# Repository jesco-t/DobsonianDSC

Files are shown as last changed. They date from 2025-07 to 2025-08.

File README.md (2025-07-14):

# Digital Setting Circles for a Manual Telescope Mount.

Design and code based on this GitHub project https://github.com/vlaate/DobsonianDSC. Code is converted to PlatformIO and a few bugs fixed (mostly due to newer dependencies having deprecated some usage patterns). A discussion thread on CloudyNights can be found here https://www.cloudynights.com/topic/589521-37-dobsonian-dsc-for-diy-makers/.

The PCB is designed for the NodeMCU DevKit C module. It is my own design.

The CAD files for the 10" Meade Lightbride are my own original design.
## PCB

The PCB is designed for the NodeMCU DevKit C. It uses 12V DC as power supply which should be readily available. It uses a 100uF input capacitor and 5V DC/DC converter to supply a stable voltage to the encoders. The ESP32 is not 5V tolerant on its GPIO pins which requires the 4-channel level shifter between NodeMCU and the encoders. 

The connectors to the encoders are JST-XH, which require a special crimp tool and some practice. The tool is extra 30€ or so but it’s well worth it in my opinion. The pinning is `+5V, GND, A, B, Shield/GND`.

The case for the board is a marginal fit because the screw holes are off by a few hundred micron. Apologies. If you want to fix it, I recommend updating the board layout in KiCAD and not the case in FreeCAD. It’s the board that has the odd measurements.

The Gerber files in the repository are suitable for JLPCB which I can highl recommend. A set of 5 boards cost me <10€.

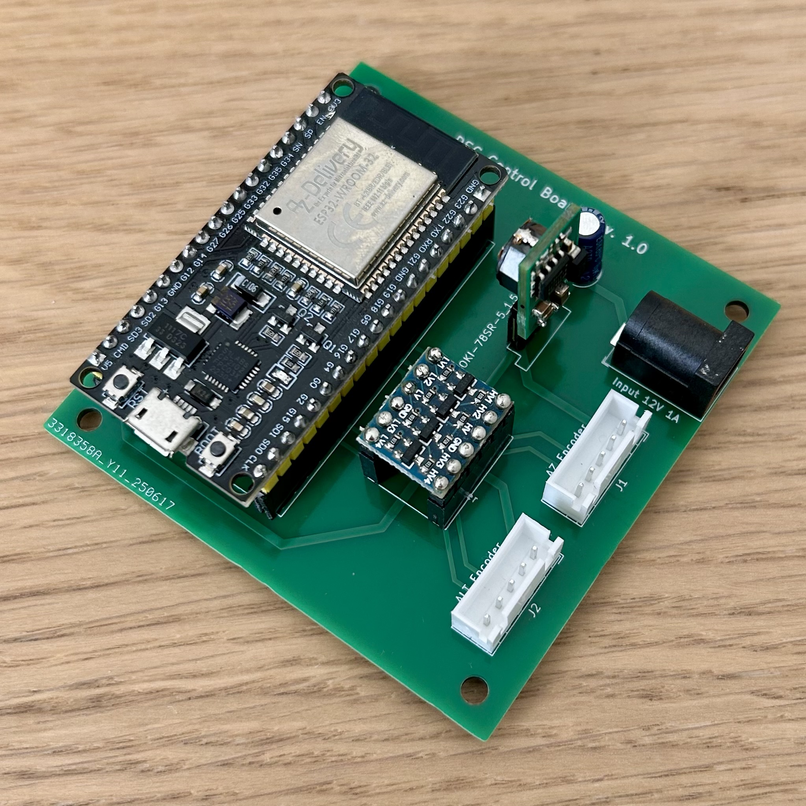
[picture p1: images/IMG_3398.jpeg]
PCB


## Software

The software needs to be compiled and uploaded with PlatformIO. Like the ArduinoIDE it's free. You need to install VSCode and the the PlatformIO extension. There are no changes needed to upload.
## Modifications on the 10" Meade Lightbridge

I use a gear driven mechanism for the encoder train. I decided against belts because the altitude axis needs to be easily to dismantle. The azimuth axis uses the same gear ratio. 

## Altitude Axis

The altitude gear is attached in three pieces: a mounting ring is glued onto the metal trunnion. The mounting ring has 4x M3 heat inserts. Then a spacer ring and the gear ring is threaded on with M3 screws.

The encoder is screwed into its mount. The encoder gear is loosely slid over the encoder and the proper spacing to the axis gear is determined. The gears should mesh well with a bit but not too much play. Mark the position and screw the encoder mount onto the base.

The axis gear has 155 teeth and the Encoder gear has 62. With 2400 pulses on the quadrature encoder this makes for 6000 steps across a 360° totation of the axis.

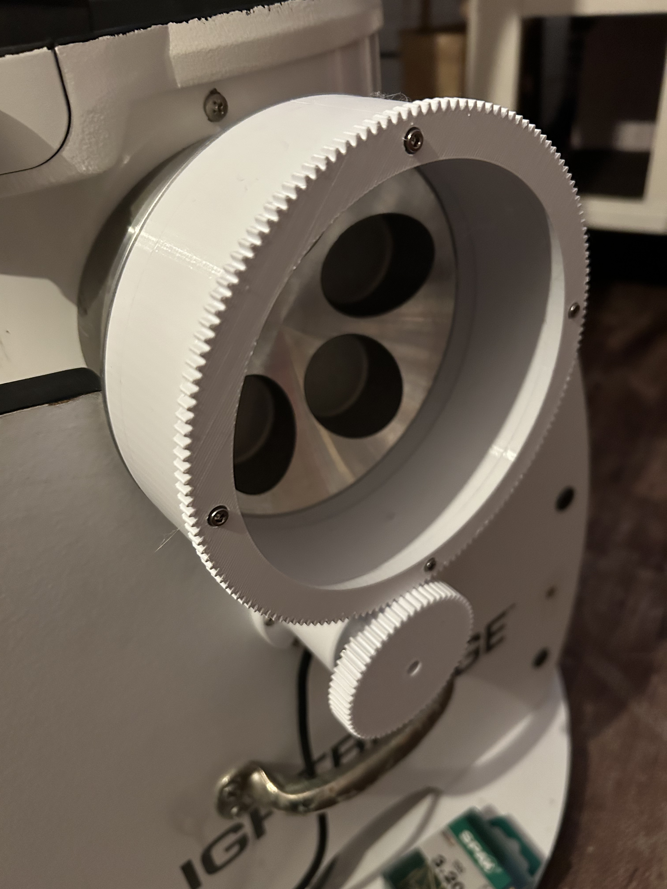
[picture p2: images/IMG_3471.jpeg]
altitude axis


## Azimuth Axis

The azimuth gear is mounted in the azimuth tension knob. It's held onto the knob with four M3 screws. The setup is the same as the altitude gear: mounting ring, spacer and then the actual gear. Here, the spacer and gear are attached with individual screws.

The encoder is attached in a similar fashion than the altitude encoder. The gear itself is mounted reverse compared to the altitude axis. For the AZ gear, use the same STL file as-is for ALT gear on the encoder. Use your slicer to remove the upper 5mm of the gear so that the height of the gear mesh is correct.

The axis gear has 155 teeth and the Encoder gear has 62. With 2400 pulses on the quadrature encoder this makes for 6000 steps across a 360° totation of the axis.

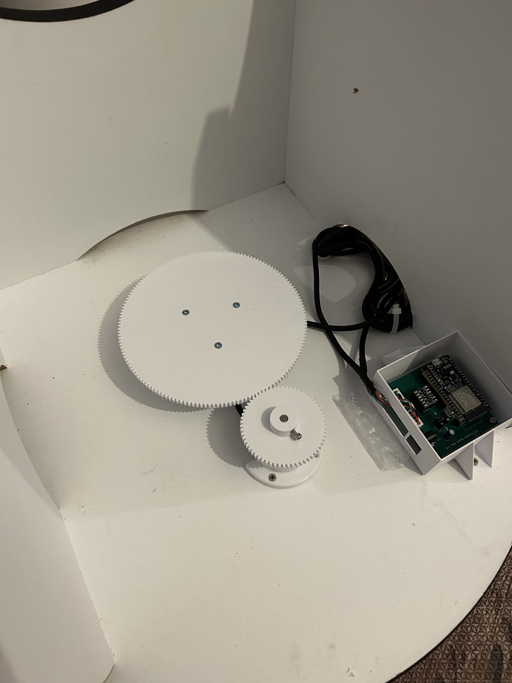
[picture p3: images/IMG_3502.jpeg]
azimuth axis


## Bill-of-Materials

| Module  | Item | Pieces | Description |
| --- | --- | --- | --- |
| PCB | NodeMCU DevKit C | 1 | |
| PCB | OKI-SR78-5/1.5-W36-C | 1 | 5V DC/DC converter |
| PCB | Capacitor (100uF/>25V) | 1 | 47uF is also ok |
| PCB | 4-Channel Level Shifter 5V~3.3V | 1 | needs VC/GND in the middle |
| PCB | JST-XH 2.54 Plug & Socket | 2 | need crimp tool also |
| PCB | 5.5x2.1 DC Socket | 1 | |
| Encoder | 600 steps A/B Encoder | 2 | |
| Misc | M3 Screw Set | 1 | |
| Misc | M3 Heat Insets | 20 | |
| Misc | 3x20 Wood Screws | 8 | |

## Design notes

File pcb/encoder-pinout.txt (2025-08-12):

Red - VCC
Black 0V
Green - A
White - B
(Yellow - Z)
(Brown - -A)
(Gray - -B)
(Orange - -Z)
Shield

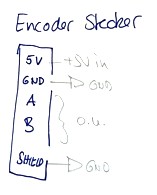
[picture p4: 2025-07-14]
pcb/encoder-pinout.jpg

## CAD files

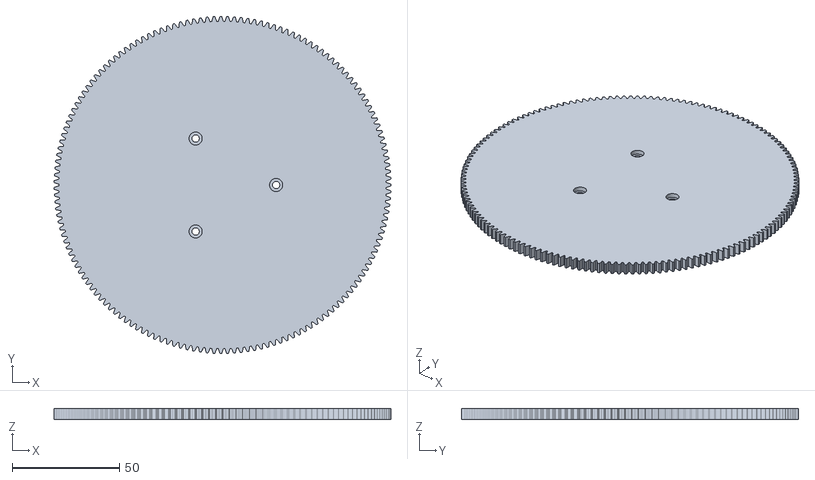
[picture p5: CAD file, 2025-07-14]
encoder_mounts/meade_lightbridge_10/AZ_Gear.stl
157.0 x 157.0 x 5.00

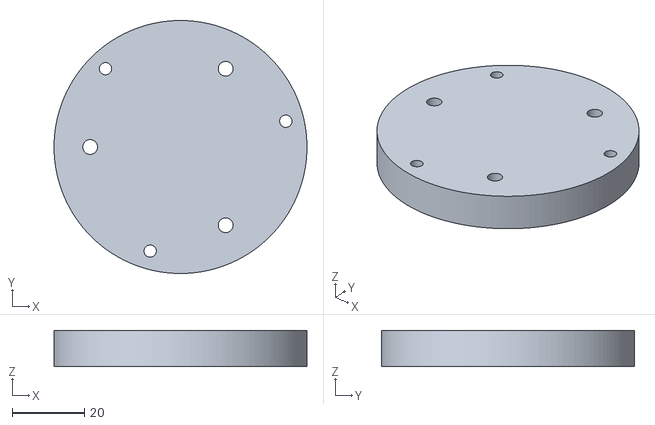
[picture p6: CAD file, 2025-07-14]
encoder_mounts/meade_lightbridge_10/STL/AZ_Spacer.stl
70.0 x 70.0 x 10.0

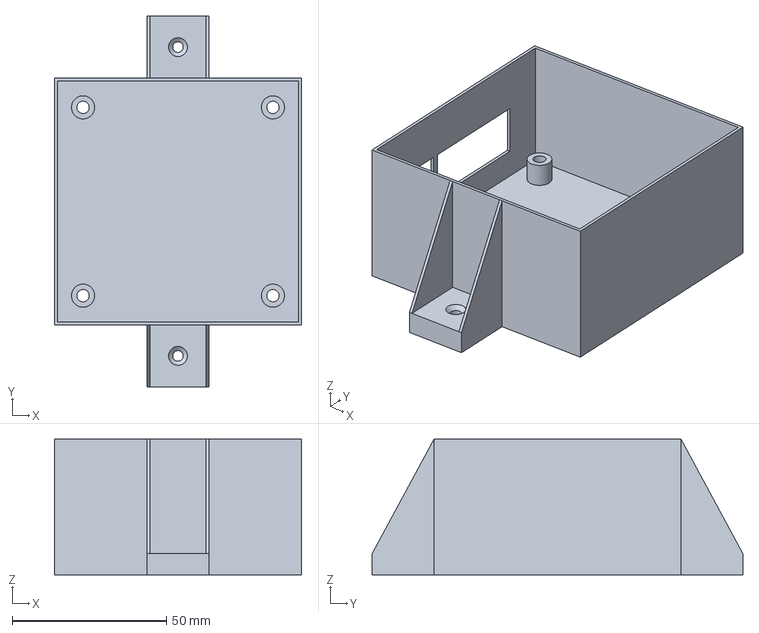
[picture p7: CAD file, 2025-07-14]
pcb/CAD/DSC-Board-Case.FCStd
80.0 x 120.0 x 44.0 mm

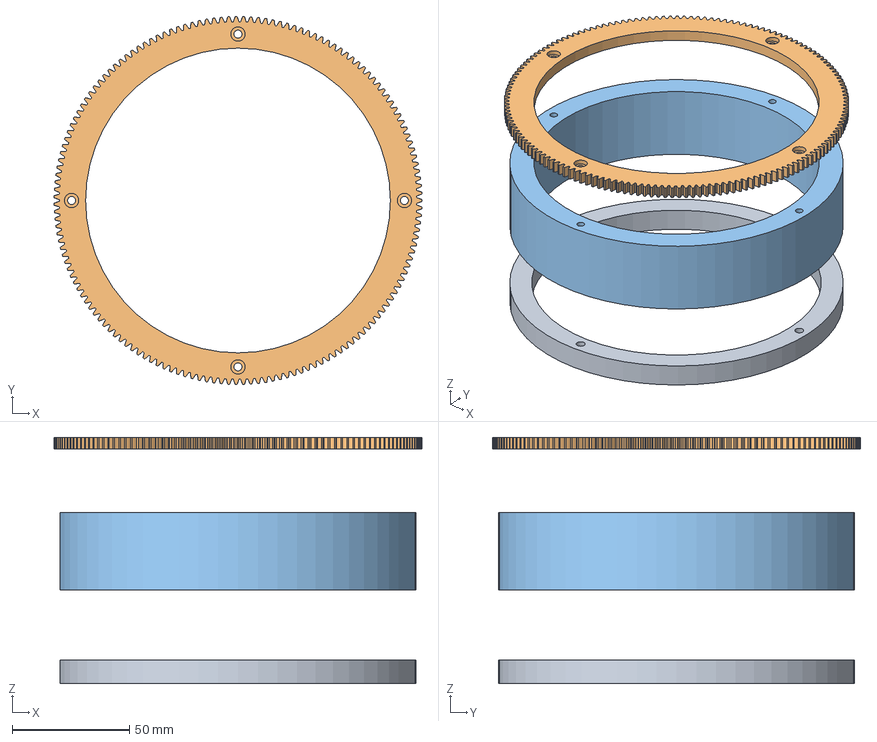
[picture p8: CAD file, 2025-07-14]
encoder_mounts/meade_lightbridge_10/ALT.FCStd
157.0 x 157.0 x 105.0 mm
Mounting
Gear
Spacer

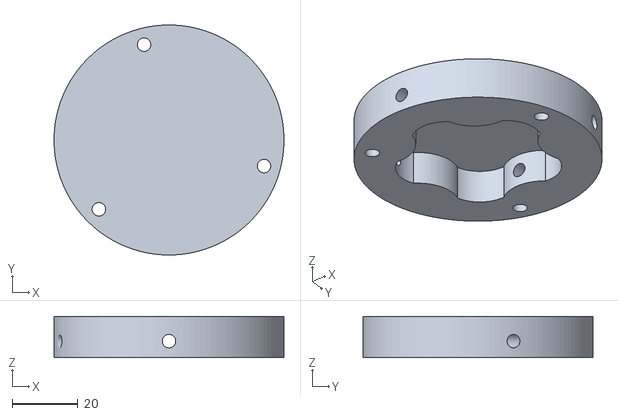
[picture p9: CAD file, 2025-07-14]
encoder_mounts/meade_lightbridge_10/STL/AZ_Mounting.stl
70.0 x 70.0 x 12.5

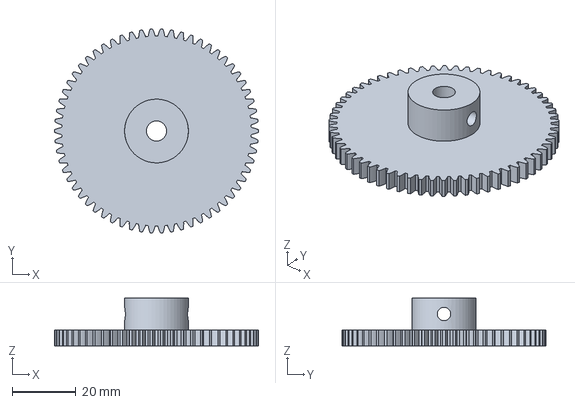
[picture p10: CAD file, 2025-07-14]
encoder_mounts/meade_lightbridge_10/ENCODER_GEAR.FCStd
64.0 x 64.0 x 15.0 mm

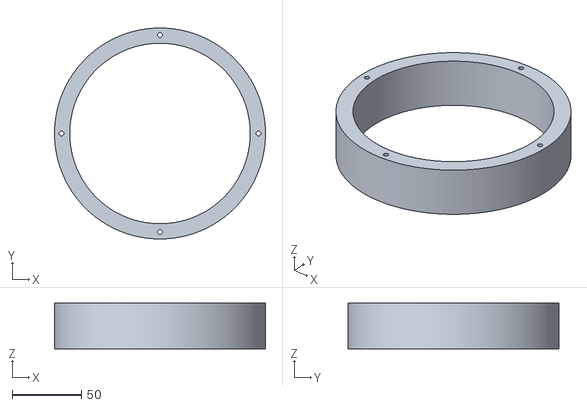
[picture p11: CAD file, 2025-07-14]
encoder_mounts/meade_lightbridge_10/STL/ALT-Spacer.stl
152.0 x 152.0 x 33.0

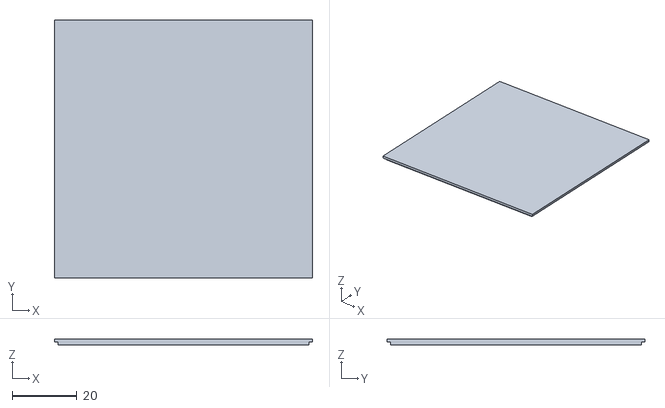
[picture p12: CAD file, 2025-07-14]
pcb/CAD/Lid.stl
80.0 x 80.0 x 2.00

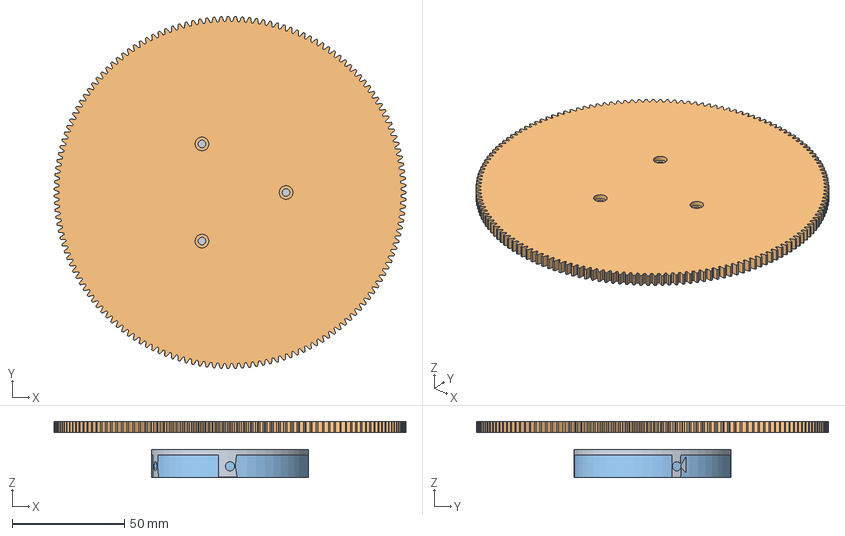
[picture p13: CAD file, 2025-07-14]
encoder_mounts/meade_lightbridge_10/AZ.FCStd
157.0 x 157.0 x 25.0 mm
AZ_Mounting
AZ_Gear
AZ_Spacer

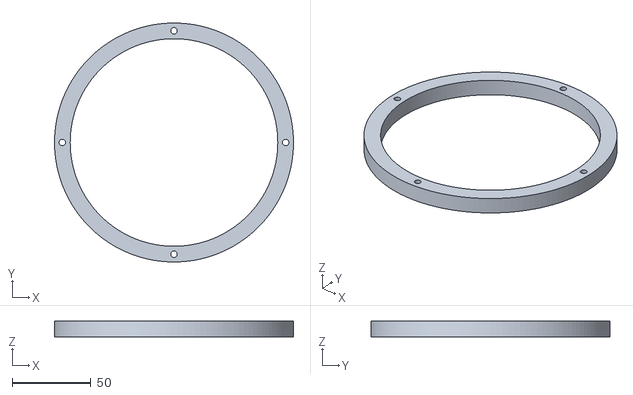
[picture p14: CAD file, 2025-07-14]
encoder_mounts/meade_lightbridge_10/STL/ALT-Mounting.stl
152.0 x 152.0 x 10.0

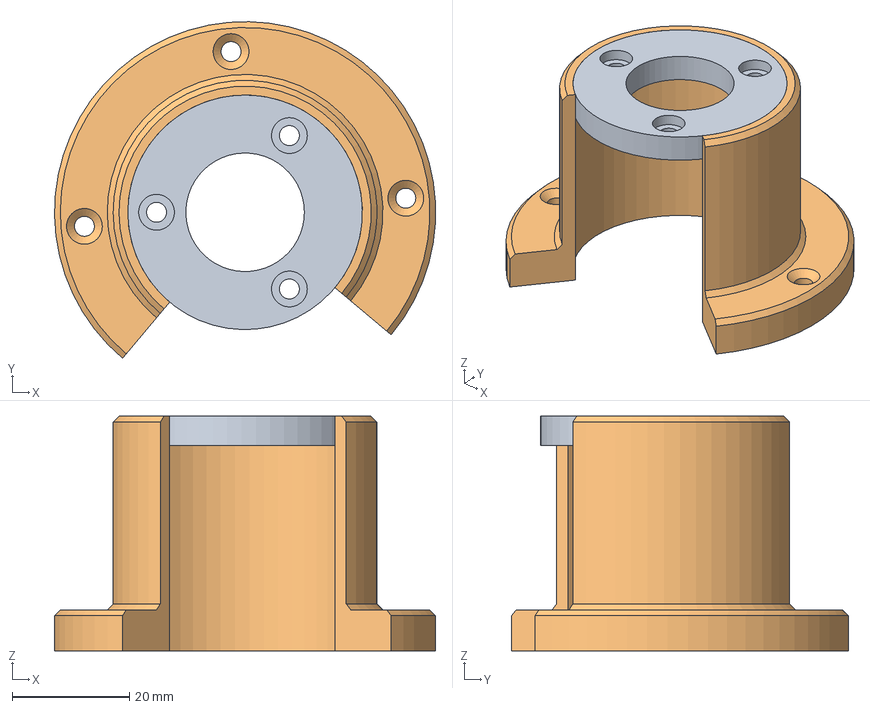
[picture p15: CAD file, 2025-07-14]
encoder_mounts/meade_lightbridge_10/ENCODER_MOUNT.FCStd
65.0 x 57.4 x 40.0 mm
Encoder_Top
alt_mount

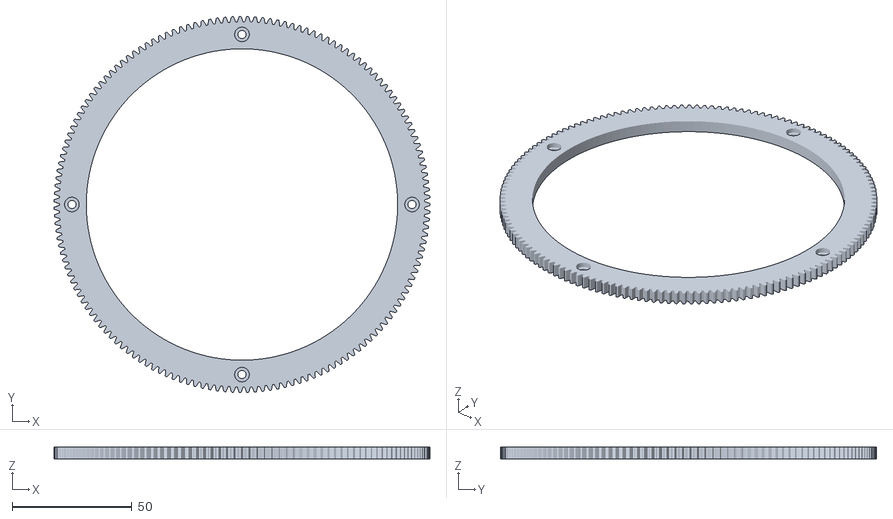
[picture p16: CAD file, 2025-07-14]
encoder_mounts/meade_lightbridge_10/STL/ALT-Gear.stl
157.0 x 157.0 x 5.00

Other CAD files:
pcb/CAD/Case.stl
encoder_mounts/meade_lightbridge_10/STL/ENCODER_MOUNT-ALT.stl
encoder_mounts/meade_lightbridge_10/STL/ENCODER_GEAR.stl

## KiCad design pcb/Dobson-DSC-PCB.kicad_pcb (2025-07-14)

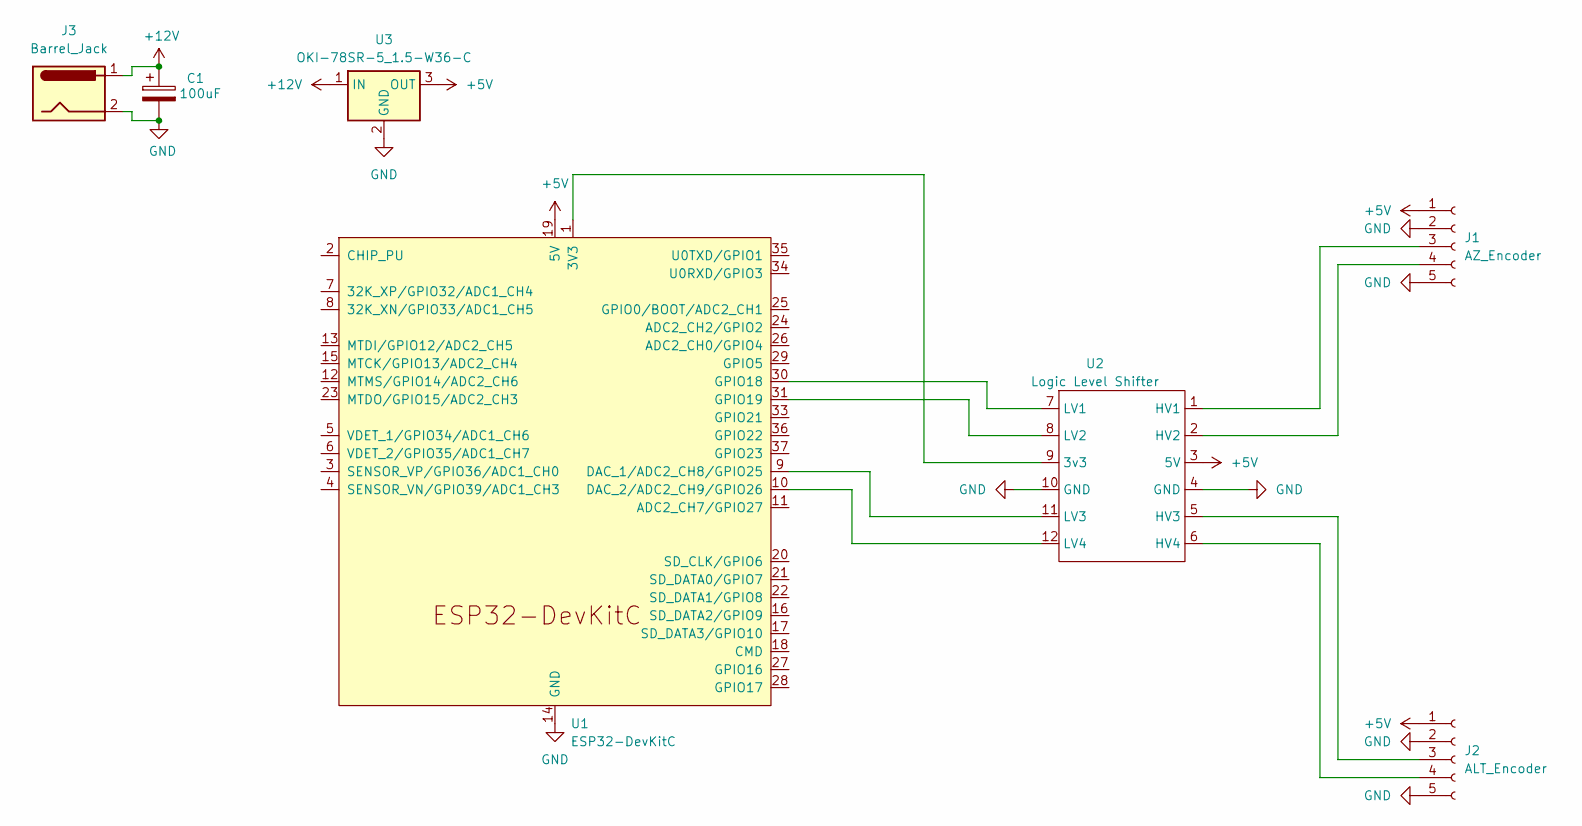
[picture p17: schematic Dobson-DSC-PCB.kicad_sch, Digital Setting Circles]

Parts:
C1: C_Polarized; CP_Radial_D5.0mm_P2.50mm
J1: AZ_Encoder; JST_XH_B5B-XH-AM_1x05_P2.50mm_Vertical
J2: ALT_Encoder; JST_XH_B5B-XH-AM_1x05_P2.50mm_Vertical
J3: Barrel_Jack; BarrelJack_Horizontal
U1: ESP32-DevKitC
U2: Logic Level Shifter; Level-Shifter 4
U3: OKI-78SR-5_1.5-W36-C; Converter_DCDC_Murata_OKI-78SR_Vertical

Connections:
+5V: J1.1, J2.1, U1.19 (5V), U2.3 (5V), U3.3 (OUT)
+12V: C1.1, J3.1, U3.1 (IN)
GND: C1.2, J1.2, J1.5, J2.2, J2.5, J3.2, U1.14 (GND), U1.32 (GND), U1.38 (GND), U2.4 (GND), U2.10 (GND), U3.2 (GND)
unnamed: J1.3, U2.1 (HV1)
unnamed: J1.4, U2.2 (HV2)
unnamed: J2.3, U2.5 (HV3)
unnamed: J2.4, U2.6 (HV4)
unnamed: U1.1 (3V3), U2.9 (3v3)
unnamed: U1.9 (DAC_1/ADC2_CH8/GPIO25), U2.11 (LV3)
unnamed: U1.10 (DAC_2/ADC2_CH9/GPIO26), U2.12 (LV4)
unnamed: U1.30 (GPIO18), U2.7 (LV1)
unnamed: U1.31 (GPIO19), U2.8 (LV2)

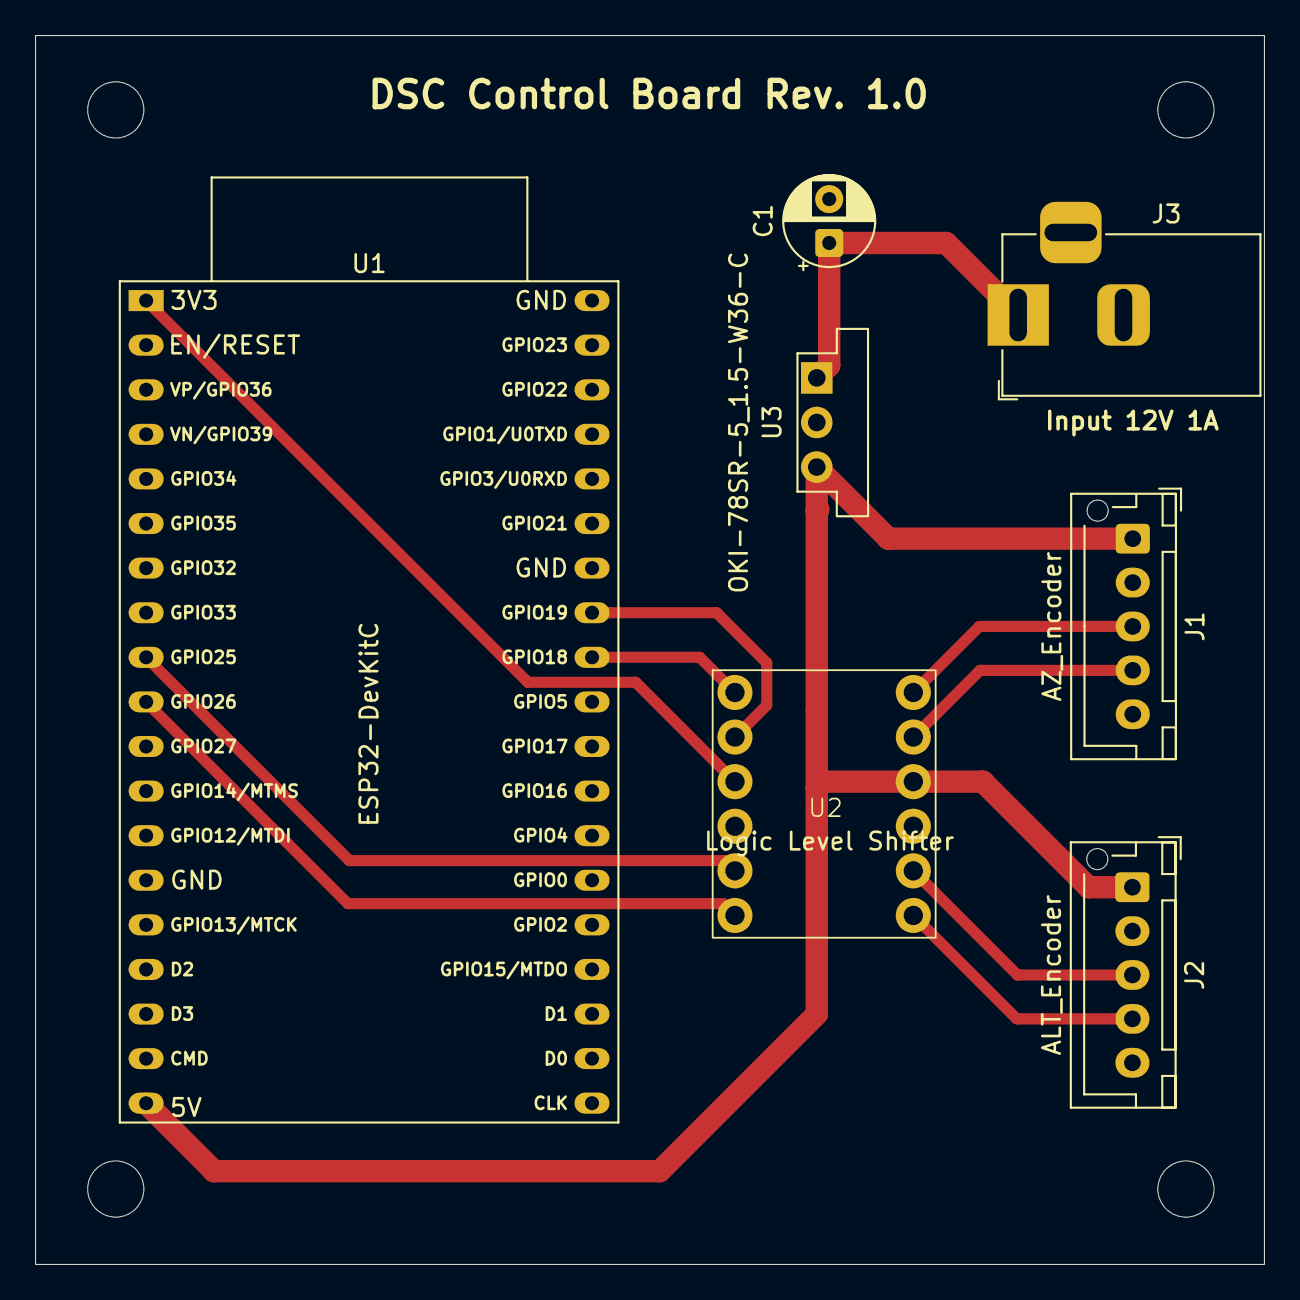
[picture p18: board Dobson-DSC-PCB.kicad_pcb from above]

Board: 2 copper layers, 70.0 x 70.0 mm, 7 parts (0 on the bottom side), 12 nets.

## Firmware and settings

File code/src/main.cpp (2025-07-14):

/*
  Dual Encoder Digital Setting Circles for ESP32 microcontrollers

  This is a simple adapter to connect two inexpensive incremental optical encoders
  via WiFi and/or BlueTooth to astronomy apps such as SkySafari,
  in order to provide "Push To" style features to dobsonian style telescope mounts.

  Copyright (c) 2017-2021 Vladimir Atehortúa. All rights reserved.

  This program is free software: you can redistribute it and/or modify
  it under the terms of the version 3 GNU General Public License as
  published by the Free Software Foundation.
  This program is distributed in the hope that it will be useful,
  but WITHOUT ANY WARRANTY; without even the implied warranty of
  MERCHANTABILITY or FITNESS FOR A PARTICULAR PURPOSE.  See the
  GNU General Public License for more details.
  You should have received a copy of the GNU General Public License along with this program.
  If not, see <http://www.gnu.org/licenses/>
*/

/**
    Hardware used:
    ESP-32S Development Board, I used a generic one: https://www.aliexpress.com/item/32800930387.html?
    Two Optical Encoders with NPN (a.k.a. "N channel") "Open Collector" (a.k.a. "open drain") output, I used some 600 p/r generic ones: https://www.aliexpress.com/item/32669741048.html
    Dupont cables or other suitable connectors.
    Power supply (could be a 5V USB power bank)

    ESP32 pinout:
     IMPORTANT: Only encoders with NPN Open collector outputs can be connected directly to the pins of the ESP32. Other encoders might require level shifters.
     AZ_Encoder_A = GPIO18 = D18  (or change it in the #define code below)
     AZ_Encoder_B = GPIO19 = D19  (or change it in the #define code below)
     ALT_Encoder_A = GPIO25 = D25 (or change it in the #define code below)
     ALT_Encoder_B = GPIO26 = D26 (or change it in the #define code below)
     VIN = Encoder VCC (and if you don't use a USB power bank, this would also connect to your 5V power source)
     GND = Encoder GND
*/

/**
   Required Additional Board Managers for the Arduino IDE (File->Preferences):
   https://dl.espressif.com/dl/package_esp32_index.json

   Required libraries for the Arduino IDE (Tools -> Manage Libraries):
   ESP32Encoder by Kevin Harrington, see https://github.com/madhephaestus/ESP32Encoder
   ArduinoJson by Benoit Blanchon, see https://arduinojson.org/
*/

#include <Arduino.h>
#include <WiFi.h>
#include <WebServer.h>
#include <ESPmDNS.h>
#include <HTTPClient.h>
#include <ESP32Encoder.h>
#include "WebConfig_DSC.h"
#include "BluetoothSerial.h"
#if !defined(CONFIG_BT_ENABLED) || !defined(CONFIG_BLUEDROID_ENABLED)
#error Bluetooth is not enabled! Please run `make menuconfig` to and enable it
#endif

#define MAX_SRV_CLIENTS         3   // How many clients can connect simultaneously to the DSC.

// Choose which pins of the ESP32 to use for the Azimuth Encoder
ESP32Encoder AZencoder;
#define PIN_AZ_A 18 // Important: Not all encoders can be connected directly to the pins of the ESP32, read more about this in the project's github page
#define PIN_AZ_B 19

// Choose which pins of the ESP32 to use for the Altitude Encoder
ESP32Encoder ALTencoder;
#define PIN_ALT_A 25
#define PIN_ALT_B 26

BluetoothSerial SerialBT;

String params = "["
                "{"
                "'name':'ssid',"
                "'label':'WiFi SSID Name',"
                "'type':" + String(INPUTTEXT) + ","
                "'default':''"
                "},"
                "{"
                "'name':'pwd',"
                "'label':'WiFi Password',"
                "'type':" + String(INPUTPASSWORD) + ","
                "'default':''"
                "},"
                "{"
                "'name':'btname',"
                "'label':'Bluetooth device Name',"
                "'type':" + String(INPUTTEXT) + ","
                "'default':'Telescope'"
                "},"
                "{"
                "'name':'azsteps',"
                "'label':'Azimuth Steps',"
                "'type':" + String(INPUTNUMBER) + ","
                "'min':1,'max':10000000,"
                "'default':'10000'"
                "},"
                "{"
                "'name':'alsteps',"
                "'label':'Altitude Steps',"
                "'type':" + String(INPUTNUMBER) + ","
                "'min':1,'max':10000000,"
                "'default':'10000'"
                "},"
                "{"
                "'name':'flpaz',"
                "'label':'Flip Azimuth',"
                "'type':" + String(INPUTCHECKBOX) + ","
                "'default':'1'"
                "},"
                "{"
                "'name':'flpalt',"
                "'label':'Flip Altitude',"
                "'type':" + String(INPUTCHECKBOX) + ","
                "'default':'1'"
                "},"
                "{"
                "'name':'apikey',"
                "'label':'Notification API Key (optional)',"
                "'type':" + String(INPUTTEXT) + ","
                "'max':35,"
                "'default':''"
                "},"
                "{"
                "'name':'userkey',"
                "'label':'Notification User Key (optional)',"
                "'type':" + String(INPUTTEXT) + ","
                "'max':35,"
                "'default':''"
                "}"
                "]";

WebServer server;
WiFiServer TCPserver(4030);                 // 4030 is the TCP port Skysafari usually expects for "Basic Encoder Systems"
WiFiClient serverClients[MAX_SRV_CLIENTS];
WebConfig conf;

// function declarations
boolean initWiFi();

// method that handles the clicks on "SAVE" and "RESET" buttons on the web config form
void handleRoot();

/**
   Configure encoders using the ESP32Encoder library by Kevin Harrington.
   This uses the ESP32's hardware pulse counters, not polling nor interrupts!
   In my tests, two encoders can get simultaneous quadrature pulses at 20Khz without missing a step.
*/
void setupEncoders();

// handle connections from SkySafari and similar software via TCP on port 4030
void attendTcpRequests();

// handle connections from SkySafari and similar software via BlueTooth
void attendBTRequests();

/**
 * Arduino main setup method
 */
void setup() {
  Serial.begin(115200);
  Serial.println(params);
  conf.setDescription(params);
  conf.readConfig();
  initWiFi();
  char dns[30];
  sprintf(dns, "%s.local", conf.getApName());
  if (MDNS.begin(dns))
  {
    Serial.println("DNS active");
  }
  server.on("/", handleRoot);
  server.begin(80); // starts web server for configuration page

  TCPserver.begin(); // starts TCP server for skysafari via WiFi

  setupEncoders();

  if (conf.getValue("btname") != "")  // starts Bluetooth service only if a name has been configured for our device
  {
    SerialBT.begin(conf.getValue("btname"));
    Serial.println("BT started");
  }
}

void loop() {
  server.handleClient();
  attendBTRequests();
  attendTcpRequests();
}

boolean initWiFi() {
  boolean connected = false;
  WiFi.mode(WIFI_STA);
  Serial.print("Connecting to ");
  Serial.print(conf.values[0]);
  Serial.println(" SSID");
  if (conf.values[0] != "") {
    WiFi.begin(conf.values[0].c_str(), conf.values[1].c_str());
    uint8_t cnt = 0;
    while ((WiFi.status() != WL_CONNECTED) && (cnt < 20)) {
      delay(500);
      Serial.print(".");
      cnt++;
    }
    Serial.println();
    if (WiFi.status() == WL_CONNECTED) {
      Serial.print("IP Adress:");
      Serial.println(WiFi.localIP());
      connected = true;
      // We can use the Pushover service to send a notification to your smartphone, an easy way to obtain the IP address that was assigned to the device:
      if (conf.getValue("apikey") != "" && conf.getValue("userkey") != "")
      {
        HTTPClient http;
        http.begin("https://api.pushover.net/1/messages.json");
        http.addHeader("Content-Type", "application/x-www-form-urlencoded");
        char _header[300];
        sprintf(_header, "token=%s&user=%s&message=Telescope-DSC connected to SSID:[%s] IP Address: [%s]", conf.getValue("apikey"), conf.getValue("userkey"), WiFi.SSID(), WiFi.localIP().toString().c_str());
        int httpResponseCode = http.POST(_header);
        http.end();
      }
    }
  }
  if (!connected) { // if unable to connect to an external WiFi, let's launch our own passwordless WiFi SSID:
    WiFi.mode(WIFI_AP);
    WiFi.softAP("Telescope_DSC", "", 1);
  }
  return connected;
}

// method that handles the clicks on "SAVE" and "RESET" buttons on the web config form
void handleRoot() {
  conf.handleFormRequest(&server);
  if (server.hasArg("SAVE"))
  {
    uint8_t cnt = conf.getCount();
    for (uint8_t i = 0; i < cnt; i++)
    {
      Serial.print(conf.getName(i));
      Serial.print(" = ");
      Serial.println(conf.values[i]);
    }
  }
}

/**
   Configure encoders using the ESP32Encoder library by Kevin Harrington.
   This uses the ESP32's hardware pulse counters, not polling nor interrupts!
   In my tests, two encoders can get simultaneous quadrature pulses at 20Khz without missing a step.
*/
void setupEncoders()
{
  // It's very important to enable pull up resistors in order to work with the NPN open collector outputs:
  ESP32Encoder::useInternalWeakPullResistors = puType::up;

  // flip the pins used by Altitude encoder if the web configuration says so:
  if (conf.getBool("flpalt"))
  {
    ALTencoder.attachFullQuad(PIN_ALT_A, PIN_ALT_B);
  }
  else
  {
    ALTencoder.attachFullQuad(PIN_ALT_B, PIN_ALT_A);
  }
  ALTencoder.setFilter(0); // filters are only needed for cheap mechanical/switch encoders such as the Keyes KY-040, not by the 600p/s encoders

  // flip the pins used by Azimuth encoder if the web configuration says so:
  if (conf.getBool("flpaz"))
  {
    AZencoder.attachFullQuad(PIN_AZ_B, PIN_AZ_A);
  }
  else
  {
    AZencoder.attachFullQuad(PIN_AZ_A, PIN_AZ_B);
  }
  AZencoder.setFilter(0); // filters are only needed for cheap mechanical/switch encoders such as the Keyes KY-040, not by the 600p/s encoders

  // set starting count value after attaching
  ALTencoder.clearCount();
  AZencoder.clearCount();
}

// handle connections from SkySafari and similar software via TCP on port 4030
void attendTcpRequests()  
{
  uint8_t i;
  // check for new clients trying to connect
  if (TCPserver.hasClient()) {
    for (i = 0; i < MAX_SRV_CLIENTS; i++) {
      // find a free or disconnected spot:
      if (!serverClients[i] || !serverClients[i].connected()) {
        if (serverClients[i]) {
          serverClients[i].stop();
        }
        serverClients[i] = TCPserver.available();
        // the new client has connected
        break;
      }
    }
    // when there are no free/disconnected spots, reject the new client:
    if (i == MAX_SRV_CLIENTS) {
      WiFiClient serverClient = TCPserver.available();
      serverClient.stop();
    }
  }

  // check what the client sends for "Basic Encoder protocol" commands:
  for (i = 0; i < MAX_SRV_CLIENTS; i++)
  {
    if (serverClients[i] && serverClients[i].connected())
    {
      if (serverClients[i].available())
      {
        char character = serverClients[i].read(); // read the first character received, usually the command
        char response[30];
        switch (character)
        {
          case 'Q':   // the Query command, sent by SkySafari and others as the "Basic Encoder protocol" to query for encoder values.
            sprintf(response, "%lld\t%lld\t\n", AZencoder.getCount(), ALTencoder.getCount());
            serverClients[i].println(response);
            break;
          case 'H':   // 'H' - request for encoder resolution, e.g. 10000-10000\n
            snprintf(response, 20, "%u-%u", conf.getInt("azsteps"), conf.getInt("alsteps"));
            serverClients[i].println(response);
            break;
        }
      }
    }
  }
}

// handle connections from SkySafari and similar software via BlueTooth
void attendBTRequests()   
{
  if (SerialBT.available()) {
    //WiFi.disconnect();
    //WiFi.mode(WIFI_OFF);

    char character = SerialBT.read();
    while (SerialBT.available())
    {
      SerialBT.read();  // flushing the buffer was necessary with Skysafari 5 Plus because it sent an initial "long" command.
    }
    Serial.print("BT: ");
    Serial.println(character);
    char response[30];
    switch (character)
    {
      case 'Q':   // the Query command, sent by SkySafari and others as the "Basic Encoder protocol" to query for encoder values.
        sprintf(response, "%lld\t%lld\t\n", AZencoder.getCount(), ALTencoder.getCount());
        Serial.print(response);
        SerialBT.println(response);
        break;
      case 'H':   // 'H' - request for encoder resolution, e.g. 10000-10000\n
        snprintf(response, 20, "%u-%u\n", conf.getInt("azsteps"), conf.getInt("alsteps"));
        Serial.print(response);
        SerialBT.println(response);
        break;
      default: SerialBT.print("\n");
    }
  }
}

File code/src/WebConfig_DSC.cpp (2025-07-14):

/*

  Original file: WebConfig.cpp version 1.4
  Author Gerald Lechner lechge@gmail.com https://github.com/GerLech
  Licensed under the GNU Lesser General Public License v3.0

  This library builds a web page with a smart phone friendly form to edit
  a free definable number of configuration parameters. The submitted data will bestored in the SPIFFS
  The library works with ESP8266 and ESP32

  It has been modified by Vladimir Atehortúa to customize the HTML styles for 
  astronomy/night use (dark background with red colors) for the Digital Setting Circles project
  which is released under the compatible GPLv3
  
  This program is free software: you can redistribute it and/or modify
  it under the terms of the version 3 GNU General Public License as
  published by the Free Software Foundation.
  This program is distributed in the hope that it will be useful,
  but WITHOUT ANY WARRANTY; without even the implied warranty of
  MERCHANTABILITY or FITNESS FOR A PARTICULAR PURPOSE.  See the
  GNU General Public License for more details.
  You should have received a copy of the GNU General Public License along with this program.
  If not, see <http://www.gnu.org/licenses/>
*/

#include "WebConfig_DSC.h"
#include <Arduino.h>
#if defined(ESP32)
  #include "SPIFFS.h"
  #include <WebServer.h>
#else
  #include <ESP8266WebServer.h>
#endif
#include <ArduinoJson.h>
#include <FS.h>

const char * inputtypes[] = {"text","password","number","date","time","range","check","radio","select","color","float"};

//HTML templates
//Template for header and begin of form
const char HTML_START[] PROGMEM =
"<!DOCTYPE HTML>\n"
"<html lang='en'>\n"
"<head>\n"
"<meta http-equiv='Content-Type' content='text/html; charset=utf-8'>\n"
"<meta name='viewport' content='width=320' />\n"
"<title>Telescope-DSC</title>\n"
"<style>\n"
"body {\n"
"  background-color: #000000;\n"
"  font-family: Arial, Helvetica, Sans-Serif;\n"
"  Color: #bb0000;\n"
"  font-size:12pt;\n"
"  width:320px;\n"
"}\n"
".titel {\n"
"font-weight:bold;\n"
"text-align:center;\n"
"width:100%%;\n"
"padding:5px;\n"
"}\n"
".zeile {\n"
"  width:100%%;\n"
"  padding:5px;\n"
"  text-align: center;\n"
"}\n"
"button {\n"
"font-size:14pt;\n"
"width:150px;\n"
"border: none;\n"
"border-radius: 4px;\n"
"margin:5px;\n"
"background-color: red;\n"
"color: black;\n"
"}\n"
"input[type] {\n"
"background-color: #ffaaaa;\n"
"border: none;\n"
"}\n"
"textarea:focus, input:focus{\n"
"outline: 2px solid red;\n"
"}\n"
"input[type=checkbox] {\n"
"filter: hue-rotate(150deg);\n"
"}\n"
"</style>\n"
"</head>\n"
"<body>\n"
"<svg style=\"fill: red; width: 50%; display: block; margin: auto;\" xmlns=\"http://www.w3.org/2000/svg\" viewBox=\"0 0 180 156\"><path d=\"M0 80.2V78l6.6-2.8-3-7.2 7.4-3.2 3 7.4 21.4-8.8.8-5.8 87.6-36.2 1-5.8C143.4 7.8 162 0 163 0c7 0 17 16.8 17 30 0 4.4-1.4 6.6-3 7.2l-37 15.4-4.6-3.6-26 10.8-.2 4.4-7.4 3 2 5c3.6 1.4 5.6 3.2 7.2 6.8l35.2 75.6-3.2 1.4-37.2-65-3.2 53h-3.2l-3.6-53L59 156l-3.2-1.4 36.4-78.8-1.4-4-7.4 3.2-3.4-3-32.4 13.4L43 82l-19.4 8zM162 9c0 9.4 7.8 23.8 12.4 23.8 1.2 0 2.4-1.2 2.4-4.8 0-8-7.6-23.2-12.4-23.2-1.4 0-2.4 1-2.4 4.2z\"/></svg>\n"
"<div id='main_div' style='margin-left:15px;margin-right:15px;'>\n"
"<div class='titel'>Telescope DSC</div>\n"
"<form method='post'>\n";

//Template for one input field
const char HTML_ENTRY_SIMPLE[] PROGMEM =
"  <div class='zeile'><b>%s</b></div>\n"
"  <div class='zeile'><input type='%s' value='%s' name='%s'></div>\n";
const char HTML_ENTRY_AREA[] PROGMEM =
"  <div class='zeile'><b>%s</b></div>\n"
"  <div class='zeile'><textarea rows='%i' cols='%i' name='%s'>%s</textarea></div>\n";
const char HTML_ENTRY_NUMBER[] PROGMEM =
"  <div class='zeile'><b>%s</b></div>\n"
"  <div class='zeile'><input type='number' min='%i' max='%i' value='%s' name='%s'></div>\n";
const char HTML_ENTRY_RANGE[] PROGMEM =
"  <div class='zeile'><b>%s</b></div>\n"
"  <div class='zeile'>%i&nbsp;<input type='range' min='%i' max='%i' value='%s' name='%s'>&nbsp;%i</div>\n";
const char HTML_ENTRY_CHECKBOX[] PROGMEM =
"  <div class='zeile'><b>%s</b><input type='checkbox' %s name='%s'></div>\n";
const char HTML_ENTRY_RADIO_TITLE[] PROGMEM =
" <div class='zeile'><b>%s</b></div>\n";
const char HTML_ENTRY_RADIO[] =
"  <div class='zeile'><input type='radio' name='%s' value='%s' %s>%s</div>\n";
const char HTML_ENTRY_SELECT_START[] PROGMEM =
" <div class='zeile'><b>%s</b></div>\n"
" <div class='zeile'><select name='%s'>\n";
const char HTML_ENTRY_SELECT_OPTION[] PROGMEM =
"  <option value='%s' %s>%s</option>\n";
const char HTML_ENTRY_SELECT_END[] PROGMEM =
" </select></div>\n";
const char HTML_ENTRY_MULTI_START[] PROGMEM =
" <div class='zeile'><b>%s</b></div>\n"
" <div class='zeile'><fieldset style='text-align:left;'>\n";
const char HTML_ENTRY_MULTI_OPTION[] PROGMEM =
"  <input type='checkbox' name='%s', value='%i' %s>%s<br>\n";
const char HTML_ENTRY_MULTI_END[] PROGMEM =
" </fieldset></div>\n";
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

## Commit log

2025-07-14 add final code from local server
    [ALT-Gear.stl, ALT-Mounting.stl, ALT-Spacer.stl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]
2025-07-14 add gear ratio and steps per revolution for both axis
2025-07-14 increase PCB case bottom
    3x20 wood screw would punch through the base board otherwise
    [Case.stl, DSC-Board-Case.FCStd]
2025-08-12 add encoder-pinout description
